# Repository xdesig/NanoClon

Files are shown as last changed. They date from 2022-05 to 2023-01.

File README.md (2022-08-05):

# NanoClon V 0.01   

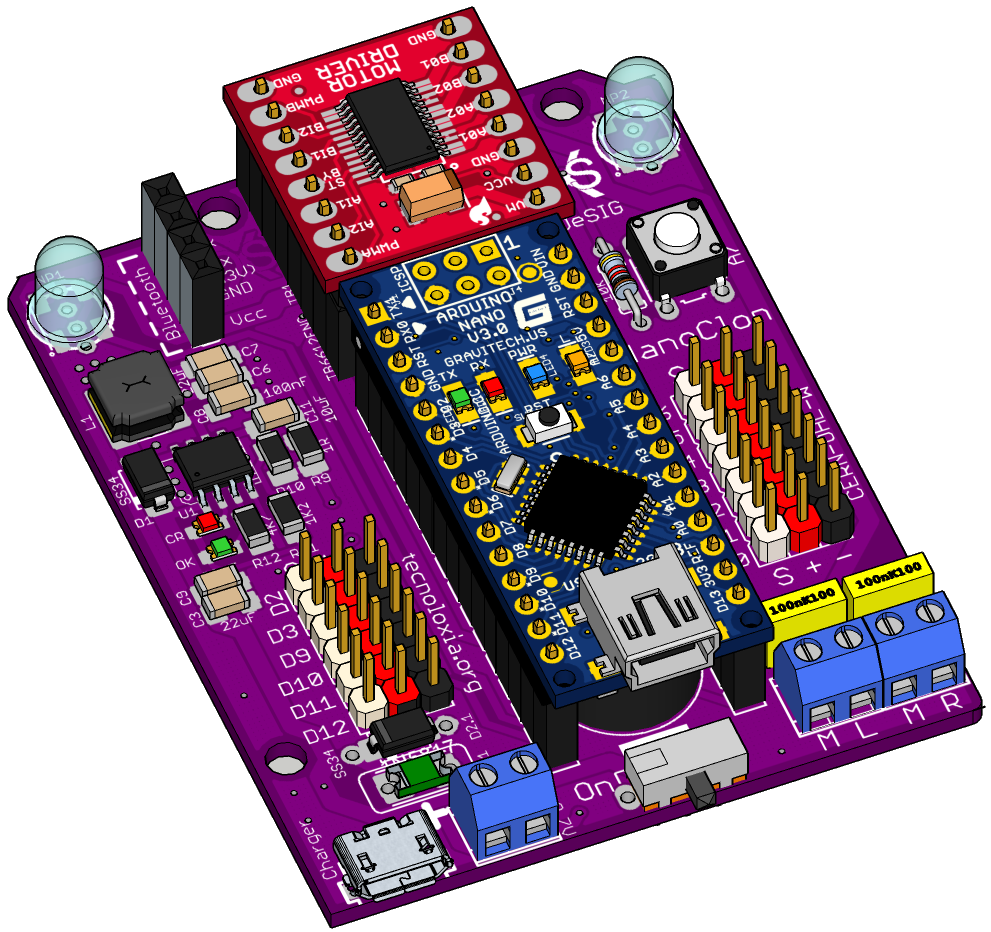
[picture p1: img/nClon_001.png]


## initial version.
Circuit that has everything you need to assemble your mClon-style robot, 
avoiding having to look for the missing Arduino one from RobotDyn that 
was used in the ShieldClon version.

The components can be SMD or THT, except for the Step-Up circuit/Lipo 
battery charge controller which is SMD,  with 1206 and 0805 components
larger than the usual 0603 and 0402).
You can an option not solder the smd components of the step-up,
and use a power bank by simply soldering the Bat-Vcc selector on the underside.

### [Assembly manual][Man]

#### Deseñado en Estrimia con agarimo.

## Author and license
* Author: [XDeSIG][TWI01]
* License:[CERN Open Hardware Licence Version 2 - Weakly Reciprocal][CERN-OHL-W]


## To buy boards

Developer don't produce boards to sell. Under [_provider_][provider]
directory there are instructions to order yourself.

<!-- links -->
[Man]: https://github.com/xdesig/NanoClon/blob/main/docs/nClon_001_Montaxe.pdf
[tecnoloxia.org]: https://tecnoloxia.org/mclon/que-e-mclon/
[CERN-OHL-W]: https://ohwr.org/cern_ohl_w_v2.pdf
[TWI01]: https://twitter.com/xdesig
[provider]: https://www.pcbway.com/project/shareproject/W50475ASJ144_NanoClon_001_gerber_f511f448.html

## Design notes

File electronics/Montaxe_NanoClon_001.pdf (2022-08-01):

# nClon

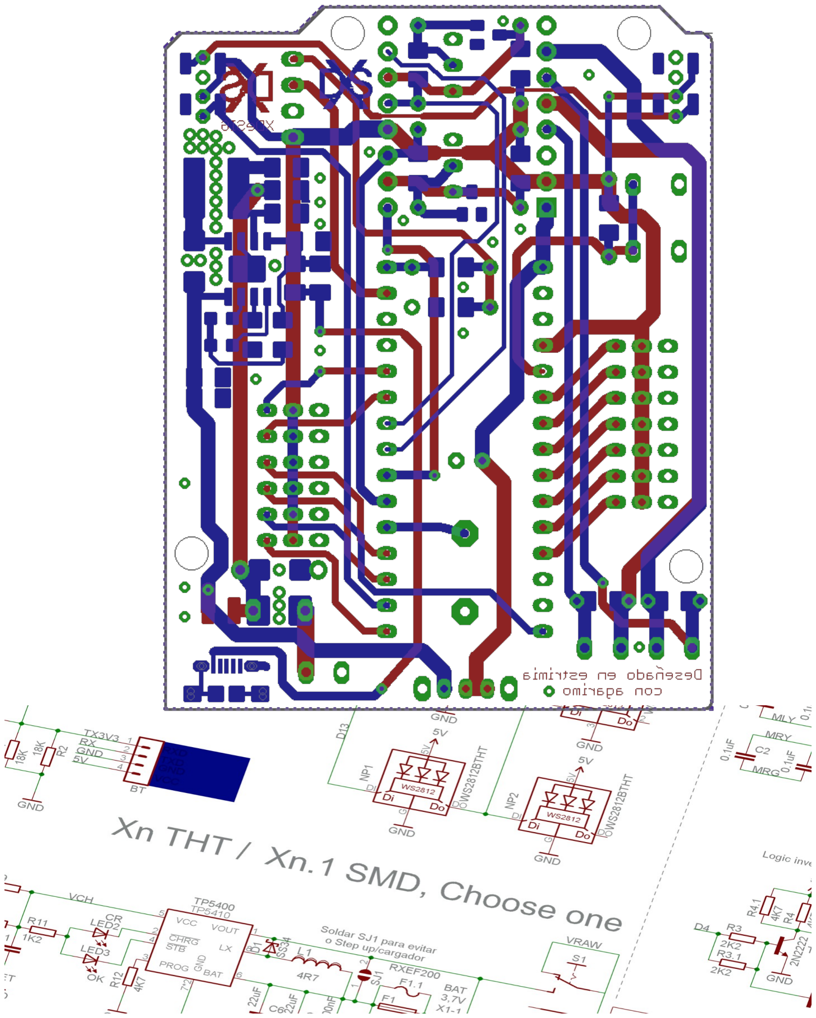
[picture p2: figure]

nClon | Manual de montaxe

Este circuíto ten todo o que precisamos () para construír o teu robot estilo mClon de @tecnoloxia, evitando ter que buscar o Arduino de RobotDyn (xa non se fabrica) que se utilizou na versión de ShieldClon.

Os compoñentes poden ser SMD ou THT, excepto o controlador de carga de batería Lipo/Step-Up que é SMD, con compoñentes 1206 e 0805 máis grandes que os habituais 0603 e 0402).
Podes optar por non soldar os compoñentes do cargador/elevador smd e usar un banco de enerxía, simplemente facendo unha pequena soldadura no selector Bat-Vcc que se atopa parte inferior.

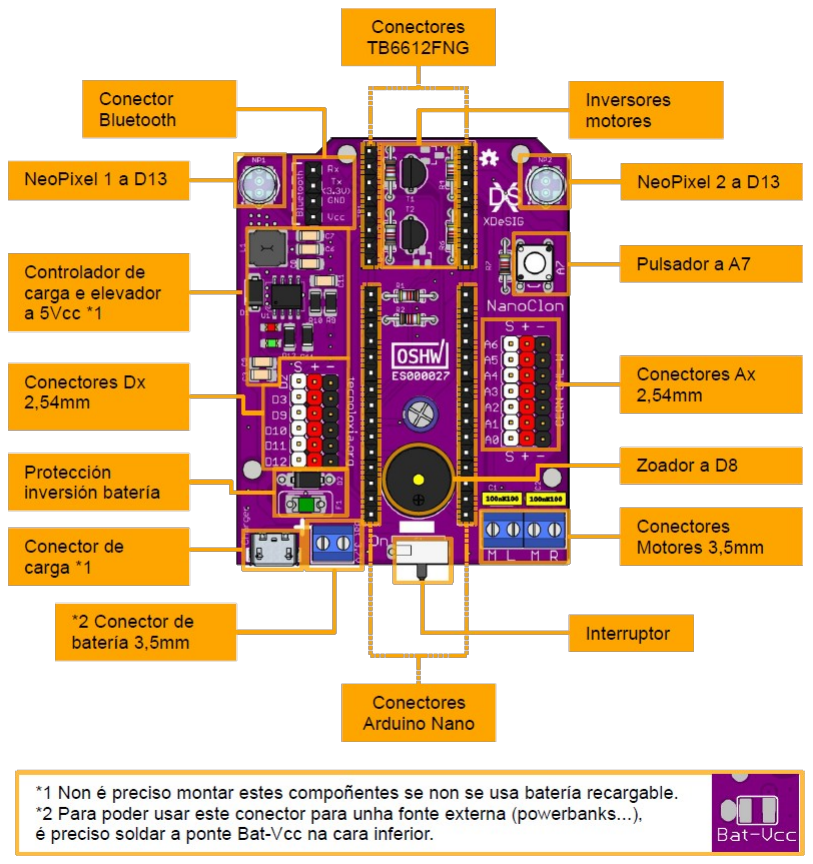
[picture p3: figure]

Podes atopar máis información en https://github.com/xdesig/NanoClon e https://tecnoloxia.org/mclon/

Deseñado en Estrimia con agarimo. | Pax. 2 de 12 | XdeSIG 2022. (CC BY-SA 4.0) Rev. 00

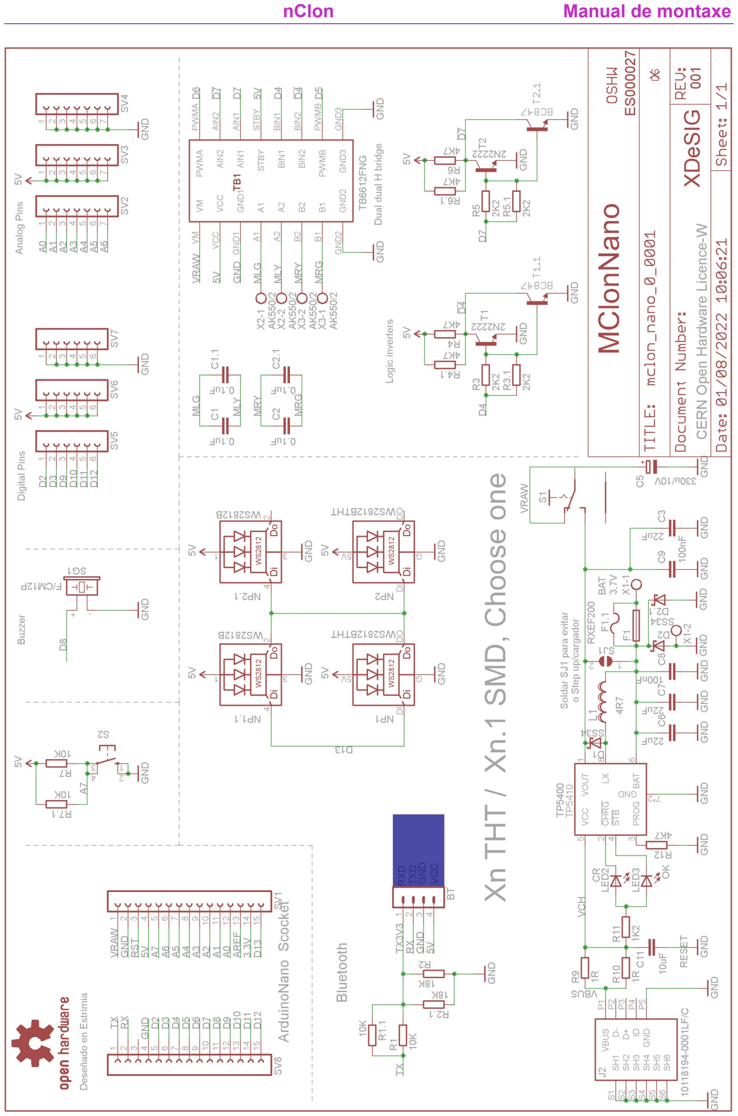
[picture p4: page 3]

Deseñado en Estrimia con agarimo. | Pax. 3 de 12 | XdeSIG 2022. (CC BY-SA 4.0) Rev. 00

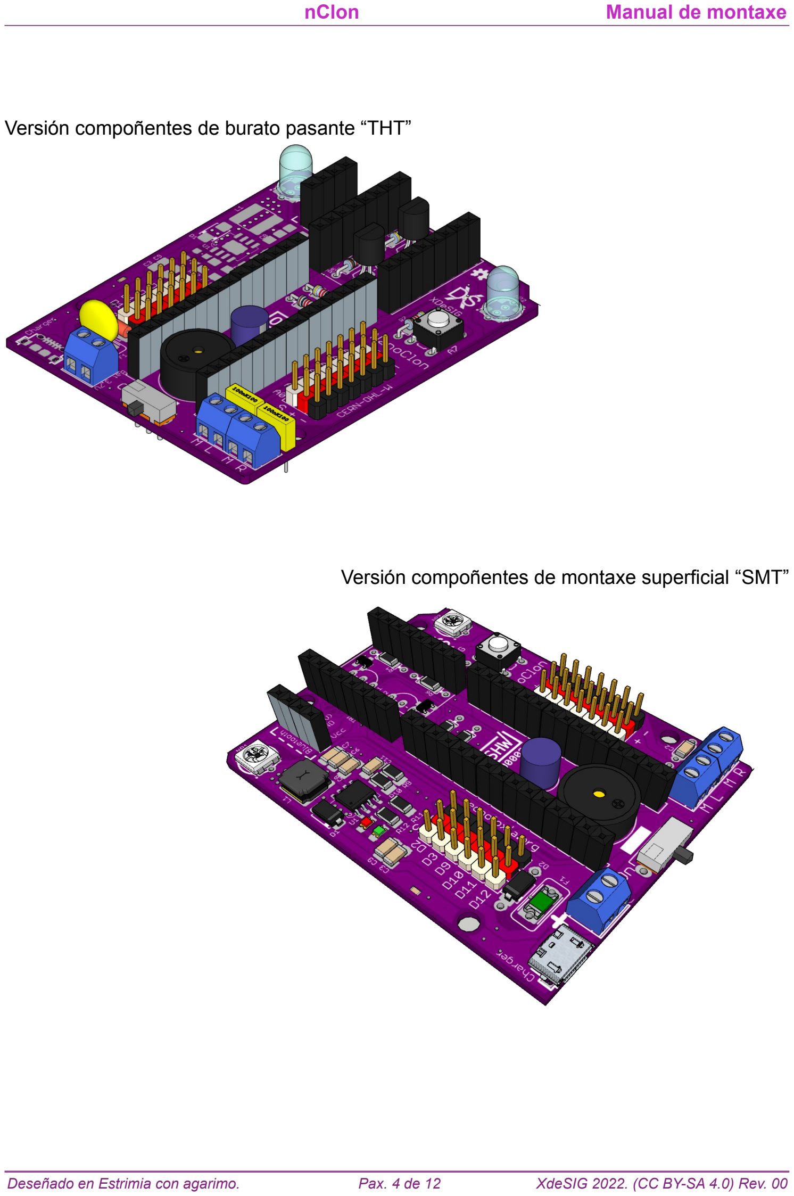
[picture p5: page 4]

Versión compoñentes de burato pasante “THT”

Versión compoñentes de montaxe superficial “SMT”

Deseñado en Estrimia con agarimo. | Pax. 4 de 12 | XdeSIG 2022. (CC BY-SA 4.0) Rev. 00

- Inventario de compoñentes comúns as dúas versións.

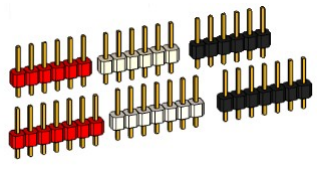
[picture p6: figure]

- Tiras de postes
- 1x 6 x 2,54mm Vermella
- 1x 6 x 2,54mm Branca
- 1x 6 x 2,54mm Negra
- 1x 7 x 2,54mm Vermella
- 1x 7 x 2,54mm Branca
- 1x 7 x 2,54mm Negra

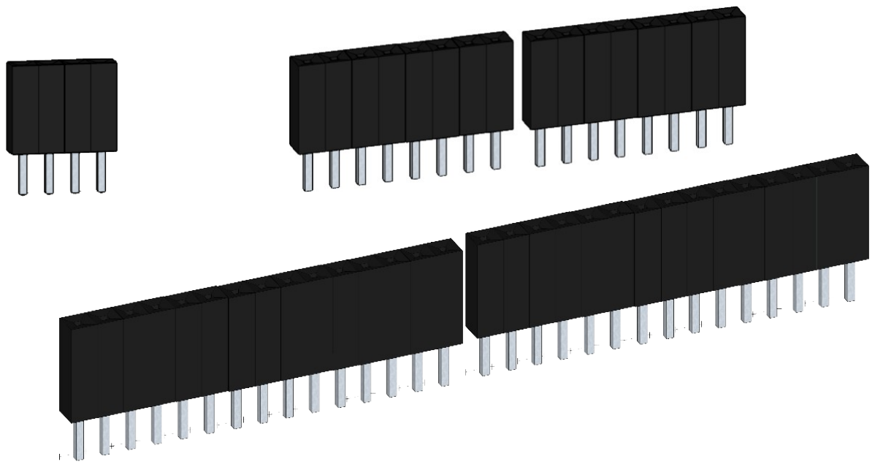
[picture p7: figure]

- Tiras Femia
- 1x 4 x 2,54mm
- 2x 8 x 2,54mm
- 2x 15 x 2,54mm
- Bloques terminais
- 3 x 2 x 3,5mm
- Interruptor SK-12D07 e pulsador 6 x 6mm

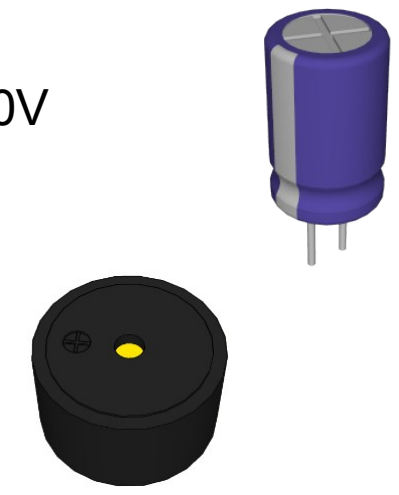
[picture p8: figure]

### - Condensador electrolítico 330µF/10V

- 6.3x7mm

### - Zoador 12mm 3,6V~5V

Deseñado en Estrimia con agarimo. | Pax. 5 de 12 | XdeSIG 2022. (CC BY-SA 4.0) Rev. 00

- Inventario de compoñentes para a versión de burato pasante “THT”
- Resistencias:
- 2x 2K2W, 2x 4K7W, 2x 10KW, 1x 18KW.
- Condensadores:
- 2x 100nF/≥16V,
- Fusible 1x Polyfuse 0,5mA
- Díodo SCHOTTKY 1N5817
- Transistores:
- 2x 2N2222
- 2x LEDes NeoPixel 5mm WS2812BTH
- Inventario de compoñentes para a versión montaxe superficial “SMD”
- Resistencias 1206:

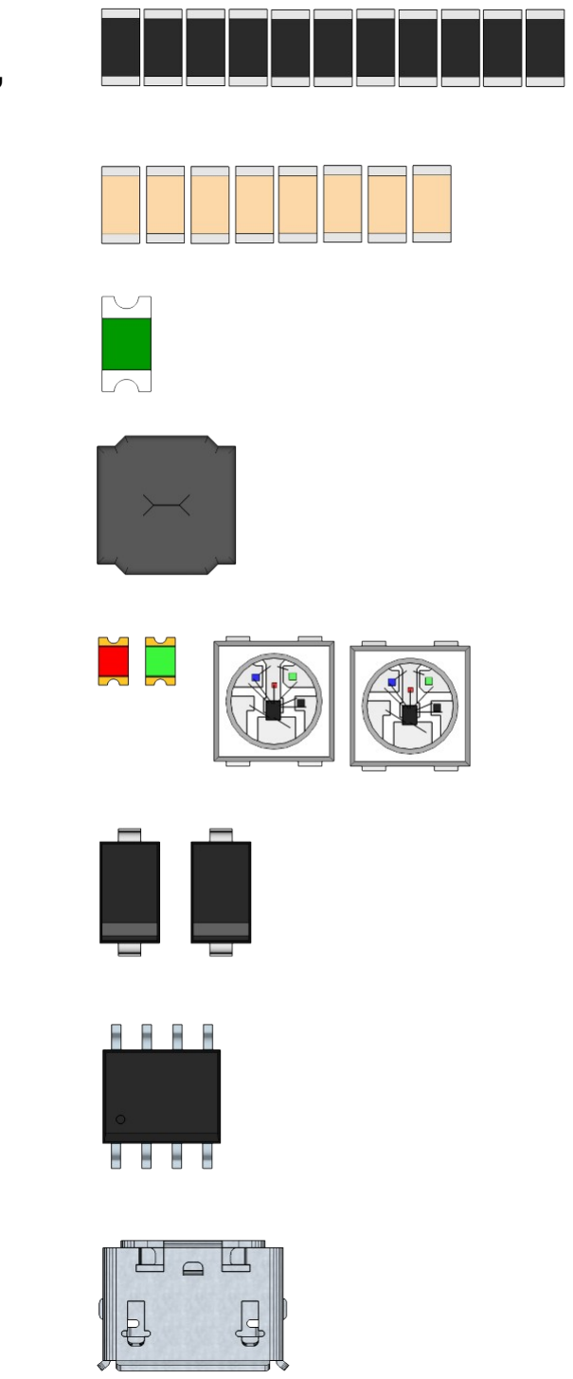
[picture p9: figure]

- 2x 1W, 1x 1K2, 1x 2K2W 3x 4K7W, 1x 18KW,
2x 10KW.
- Condensadores 1206:
- 4x 100nF, 3x 22uF/10V, 1x10uF/10V
- Fusible rearmable 1206/1210.
- MF-NSMF200-2
- Indutancia SMD 6x6mm:
- 4R7(4.7uH ±30% )
- LEDes:
- 2x LED 0805:
- Vermello e verde
- 2x NeoPixeles WS2812B
- Díodos SCHOTTKY SMA:
- 2x SS34
- Controlador batería/Step-Up SOIC-8
- 1x TP5400.
- Conector USB
- MicroXNJ .
Deseñado en Estrimia con agarimo. | Pax. 6 de 12 | XdeSIG 2022. (CC BY-SA 4.0) Rev. 00

- Módulos:
- Ponte “H” Dual
- Arduino Nano
- PCB

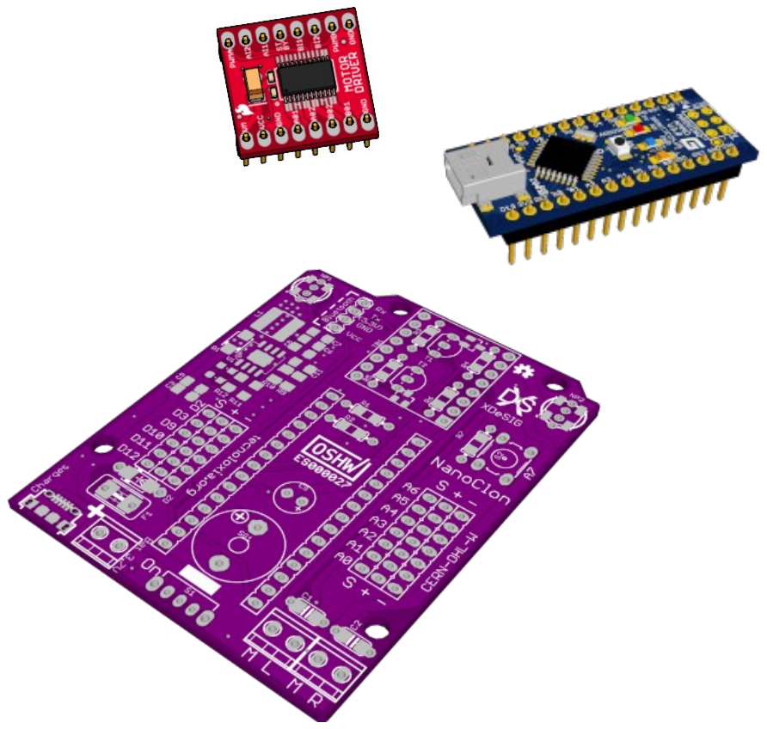
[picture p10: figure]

Primeiro imos montar a versión de compoñentes de burato pasante THT

- A montaxe, comeza polos compoñentes de baixo perfil, as resistencias. A placa vén serigrafíada cos valores dos compoñentes.
Vai soldando unha a unha as resistencias, orientadas de tal forma que sexan fáciles de ler, deixando a banda de tolerancia na dereita (a máis separada), vai cortando o sobrante das patas cada vez que soldes unha resistencia.
- OLLO As cores representadas nas resistencias non se corresponden co seu Valor

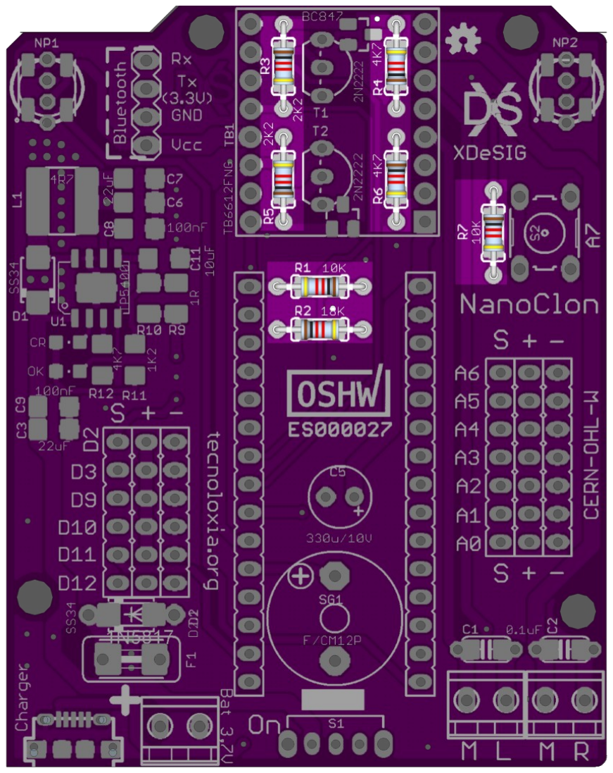
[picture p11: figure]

Deseñado en Estrimia con agarimo. | Pax. 7 de 12 | XdeSIG 2022. (CC BY-SA 4.0) Rev. 00

- Pasamos a soldar o díodo D2 Schottky 1N5817 ou compatible, este compoñente ten polaridade, faremos coincidir a liña que marca o cátodo coa marca da serigrafía:
- Na placa atopamos textos como D2... e D2 o primeiro refírese o sinal dixital do Arduino, o

segundo o atopamos o lado do compoñente 1N5817, indicando que é o Díodo 2...

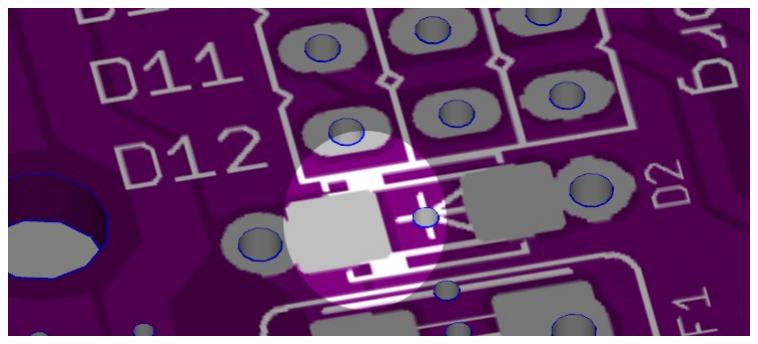
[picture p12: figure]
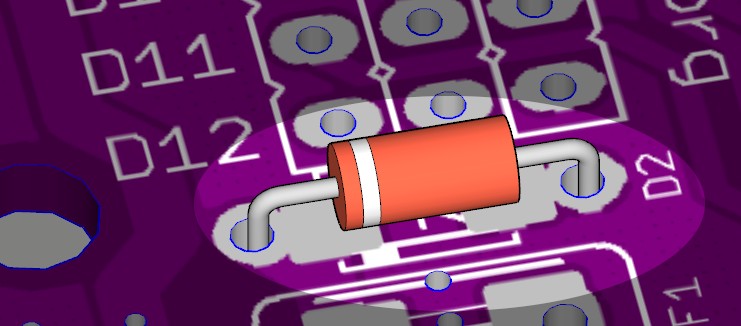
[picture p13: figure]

O soldar os semicondutores teremos que ter coidado de non aplicar moito calor

durante moito tempo, estes só aguantan uns 300º durante 10 segundos como máximo.

- Continuamos soldando o interruptor e o pulsador, estes non teñen polaridade

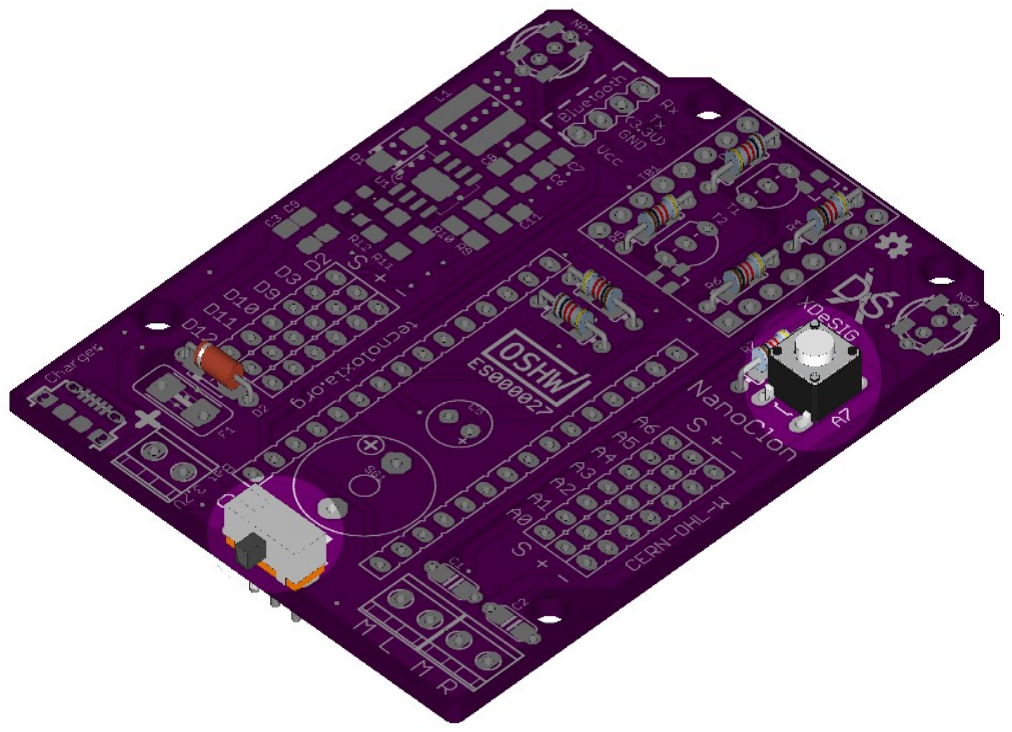
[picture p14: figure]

O pulsador, so ten unha orientación.

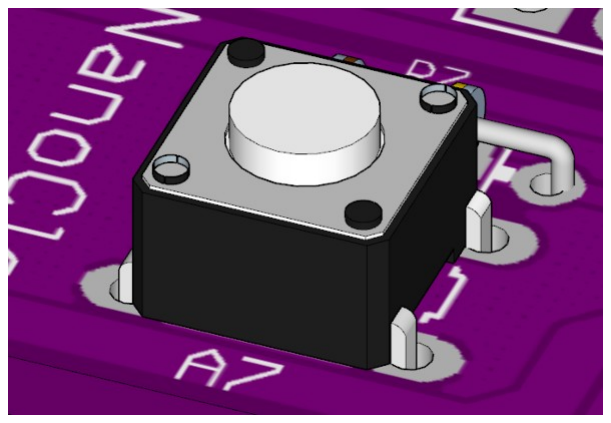
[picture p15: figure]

Deseñado en Estrimia con agarimo. | Pax. 8 de 12 | XdeSIG 2022. (CC BY-SA 4.0) Rev. 00

- Soldamos agora as tiras de postes, prestando atención as cores e que queden verticais:

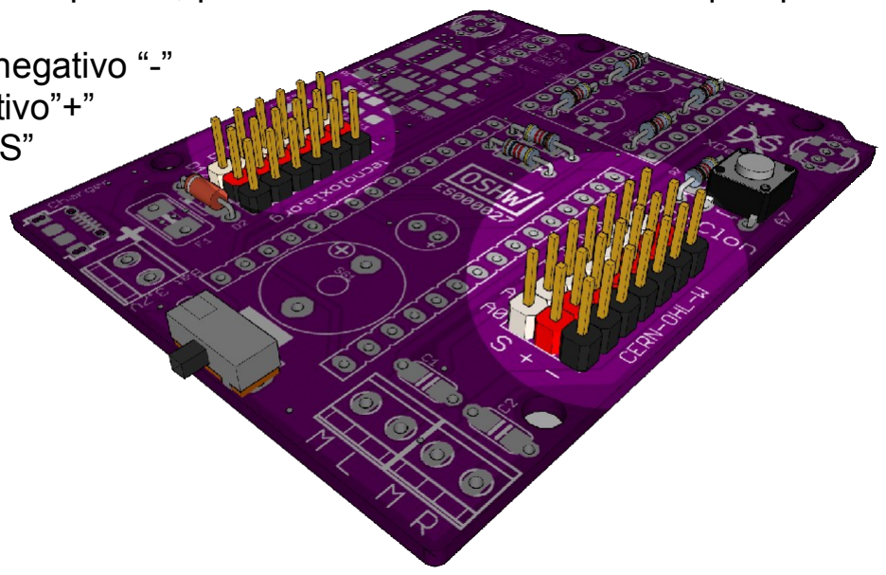
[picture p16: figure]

- Negro(preto) para o negativo “-”
- Vermello para o positivo”+”
- Branco para o sinal “S”
- Seguidamente soldamos os transistores T1 e T2, atentos a serigrafía, e coidade de non pasarnos ca calor e tempo de soldadura.
- Consello: Solda unha pata de un transistor, e mentas soldas a do outro, este arrefriase un pouco.

Só aguantan uns 300º durante 10 segundos

como máximo.

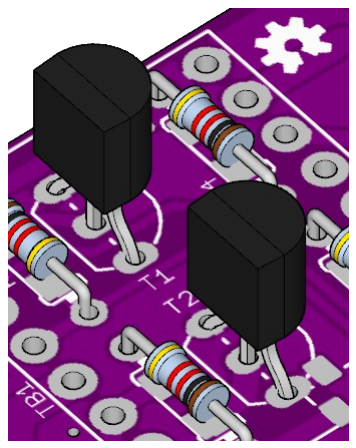
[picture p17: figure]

- Antes de continuar comproba que o condensador C5 non é máis alto que as tiras de conexión do Arduino. No caso de que sexa máis alto teremos que soldalo tumbado no seguinte paso
- Soldamos o condensador C5, este compoñente ten polaridade.
Na placa ven marcada a pata positiva ”+”, pero o condensador ten marcada

(xeralmente) a pata negativa “-” con unha franxa.

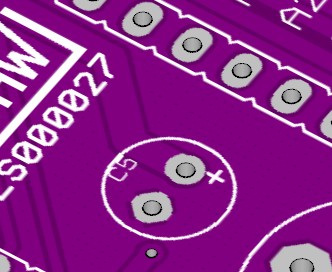
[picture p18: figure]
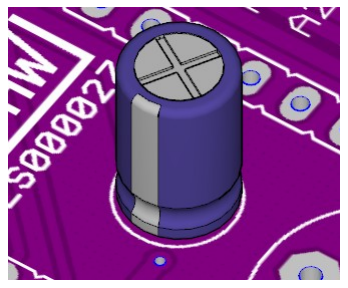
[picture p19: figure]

Deseñado en Estrimia con agarimo. | Pax. 9 de 12 | XdeSIG 2022. (CC BY-SA 4.0) Rev. 00

- E soldamos o coador que tamén ten polaridade, este ten marcada a pata positiva (+)

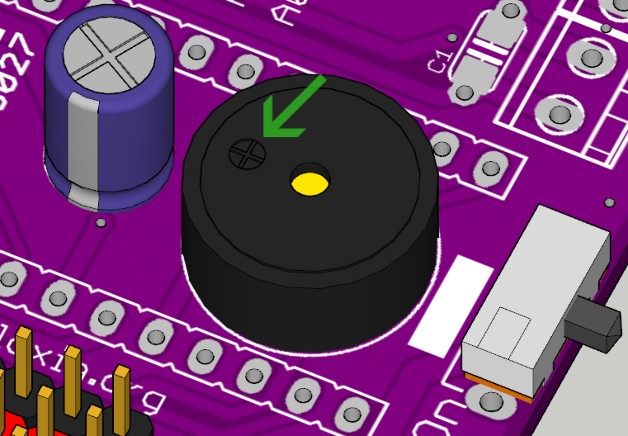
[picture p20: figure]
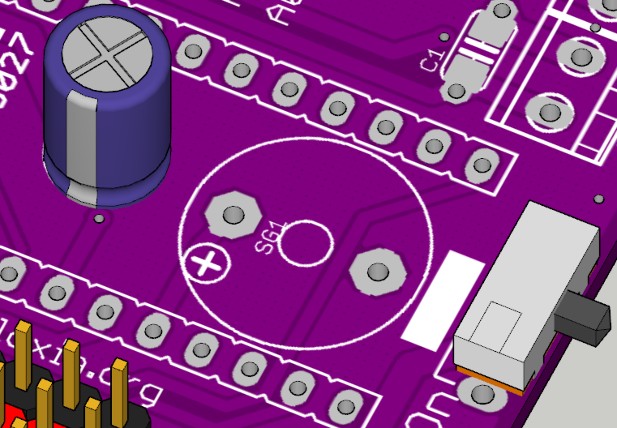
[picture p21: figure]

- Xa podemos soldar os conectores da batería e motores, non teñen polaridade, pero deixa a entrada do cable o borde da placa ;-).

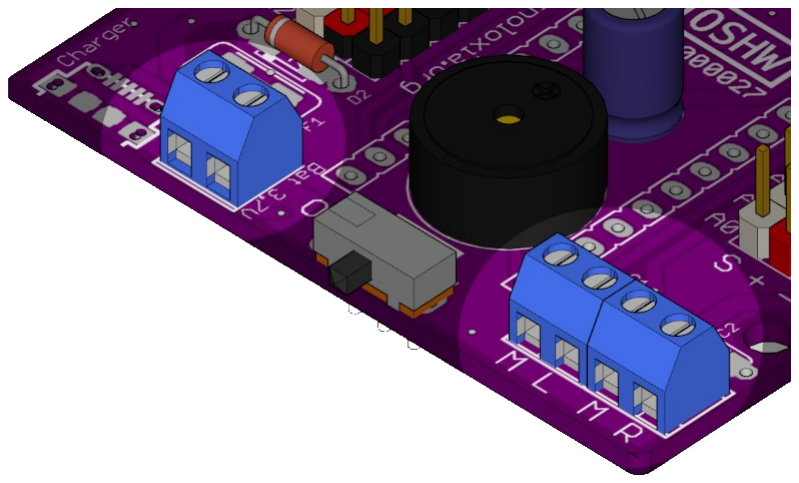
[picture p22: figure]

- Soldaremos agora fusible rearmable e os condensadores dos motores.

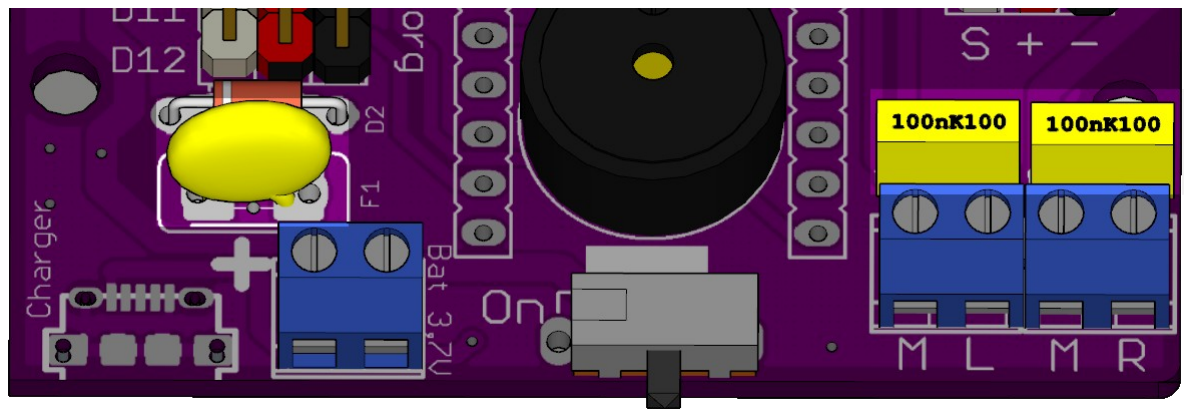
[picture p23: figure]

Deseñado en Estrimia con agarimo. | Pax. 10 de 12 | XdeSIG 2022. (CC BY-SA 4.0) Rev. 00

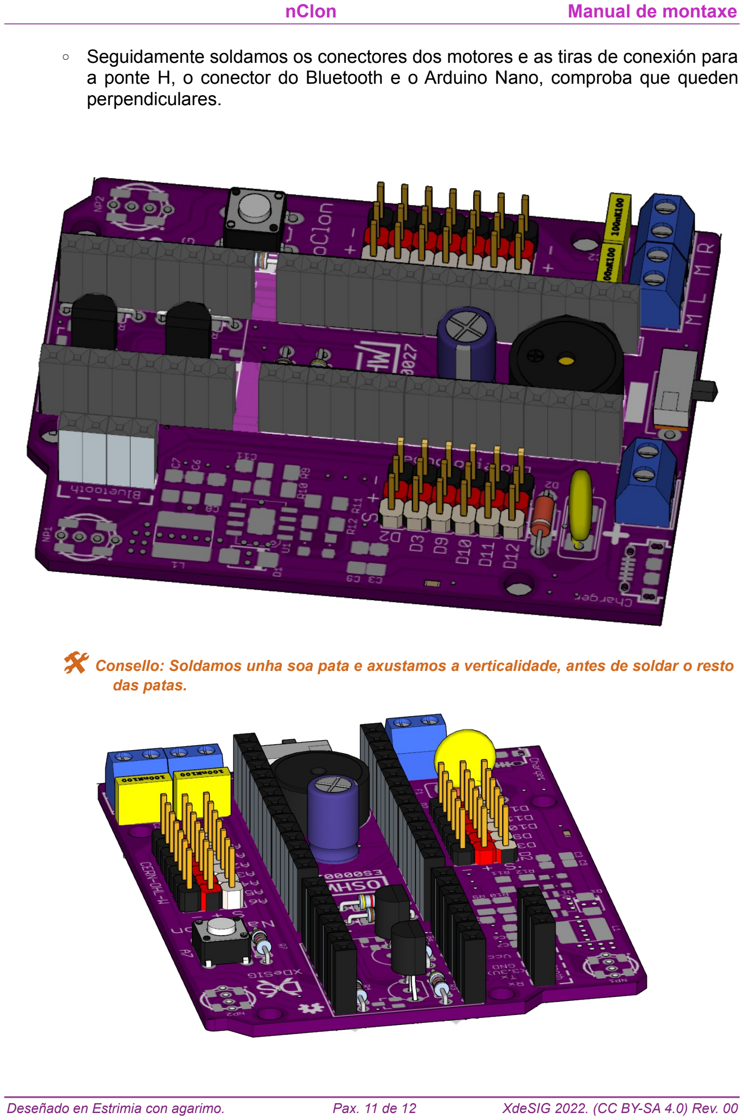
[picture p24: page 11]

- Seguidamente soldamos os conectores dos motores e as tiras de conexión para a ponte H, o conector do Bluetooth e o Arduino Nano, comproba que queden perpendiculares.
- Consello: Soldamos unha soa pata e axustamos a verticalidade, antes de soldar o resto das patas.
Deseñado en Estrimia con agarimo. | Pax. 11 de 12 | XdeSIG 2022. (CC BY-SA 4.0) Rev. 00

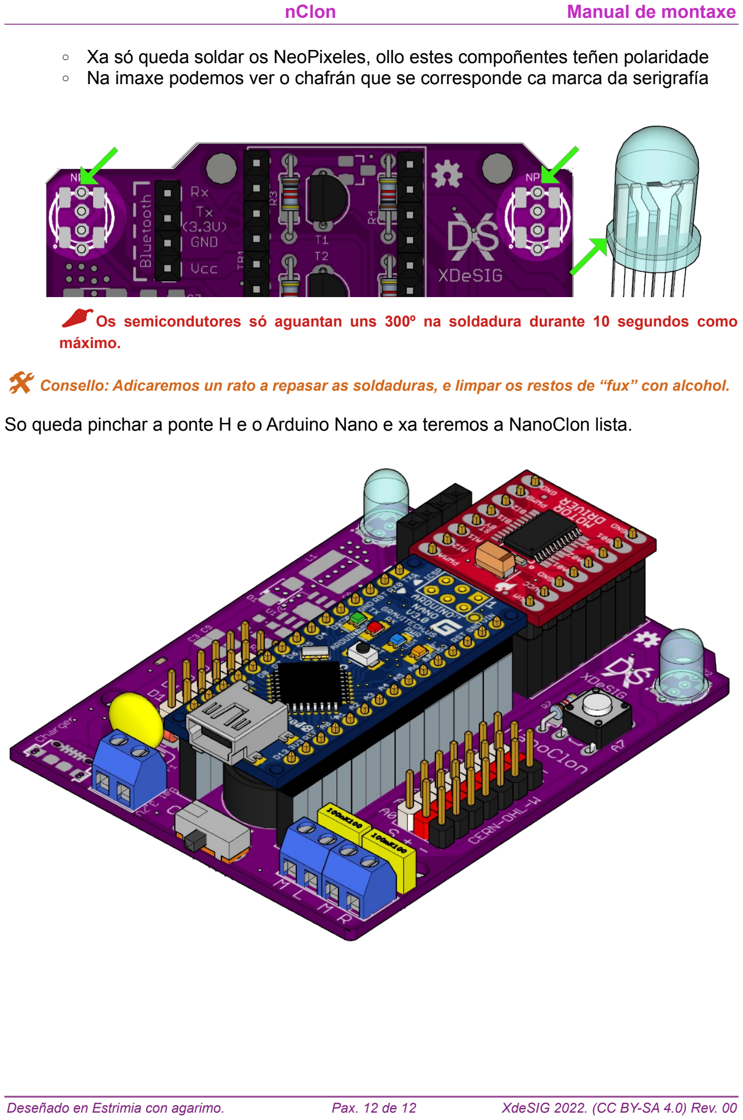
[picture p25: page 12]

- Xa só queda soldar os NeoPixeles, ollo estes compoñentes teñen polaridade
- Na imaxe podemos ver o chafrán que se corresponde ca marca da serigrafía

Os semicondutores só aguantan uns 300º na soldadura durante 10 segundos como

máximo.

- Consello: Adicaremos un rato a repasar as soldaduras, e limpar os restos de “fux” con alcohol.

So queda pinchar a ponte H e o Arduino Nano e xa teremos a NanoClon lista.

Deseñado en Estrimia con agarimo. | Pax. 12 de 12 | XdeSIG 2022. (CC BY-SA 4.0) Rev. 00

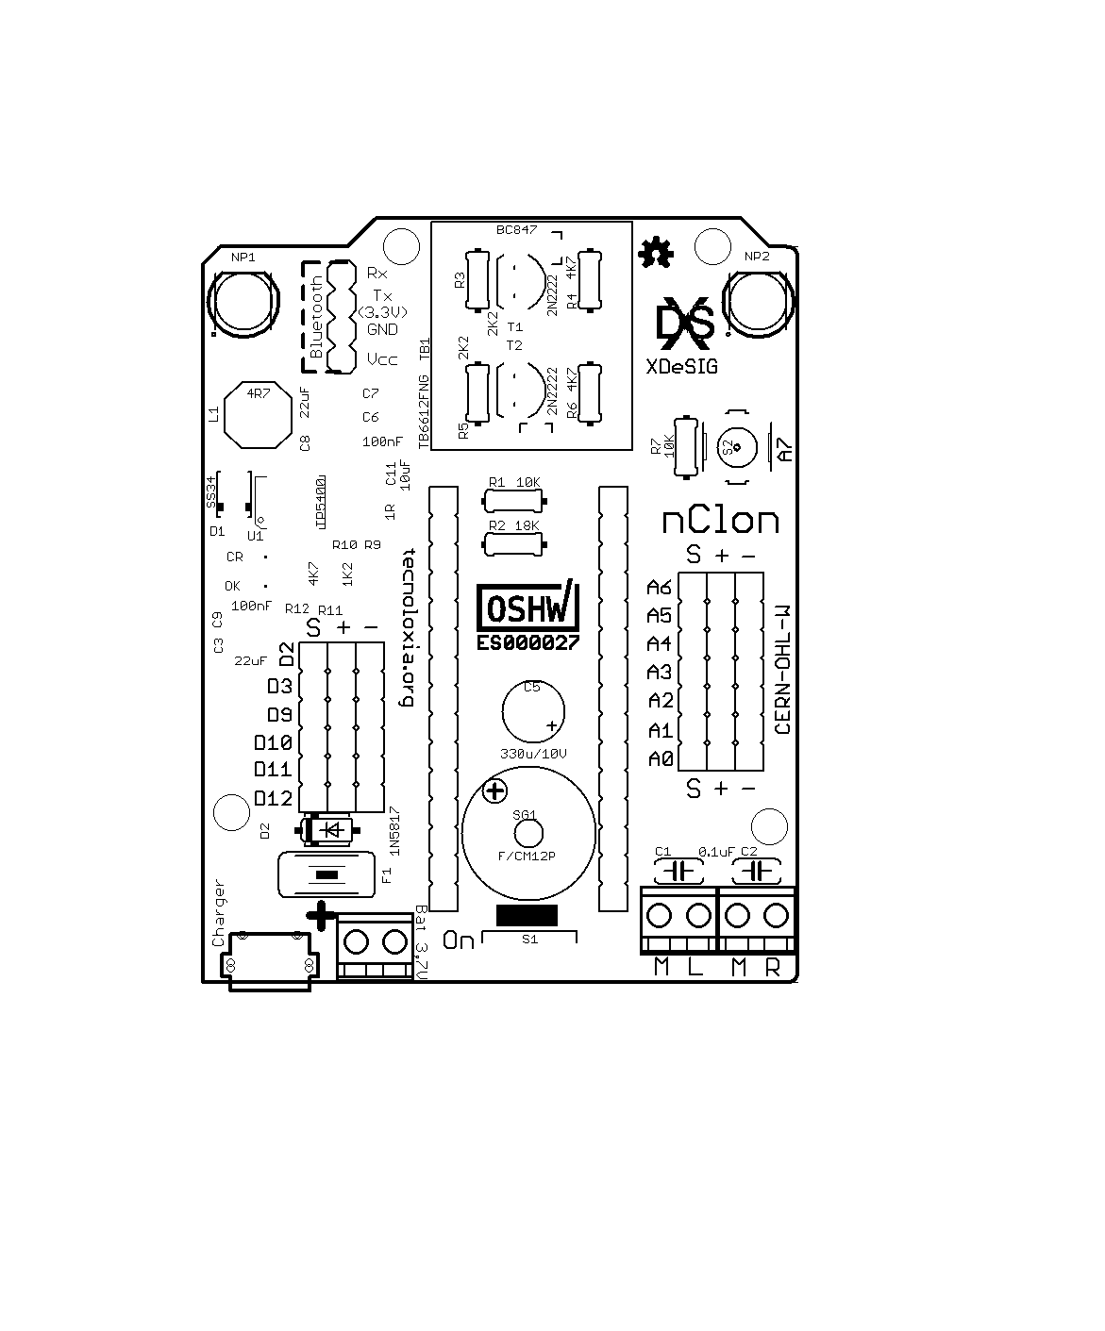
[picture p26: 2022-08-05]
img/nClon_001_SilkTop.png

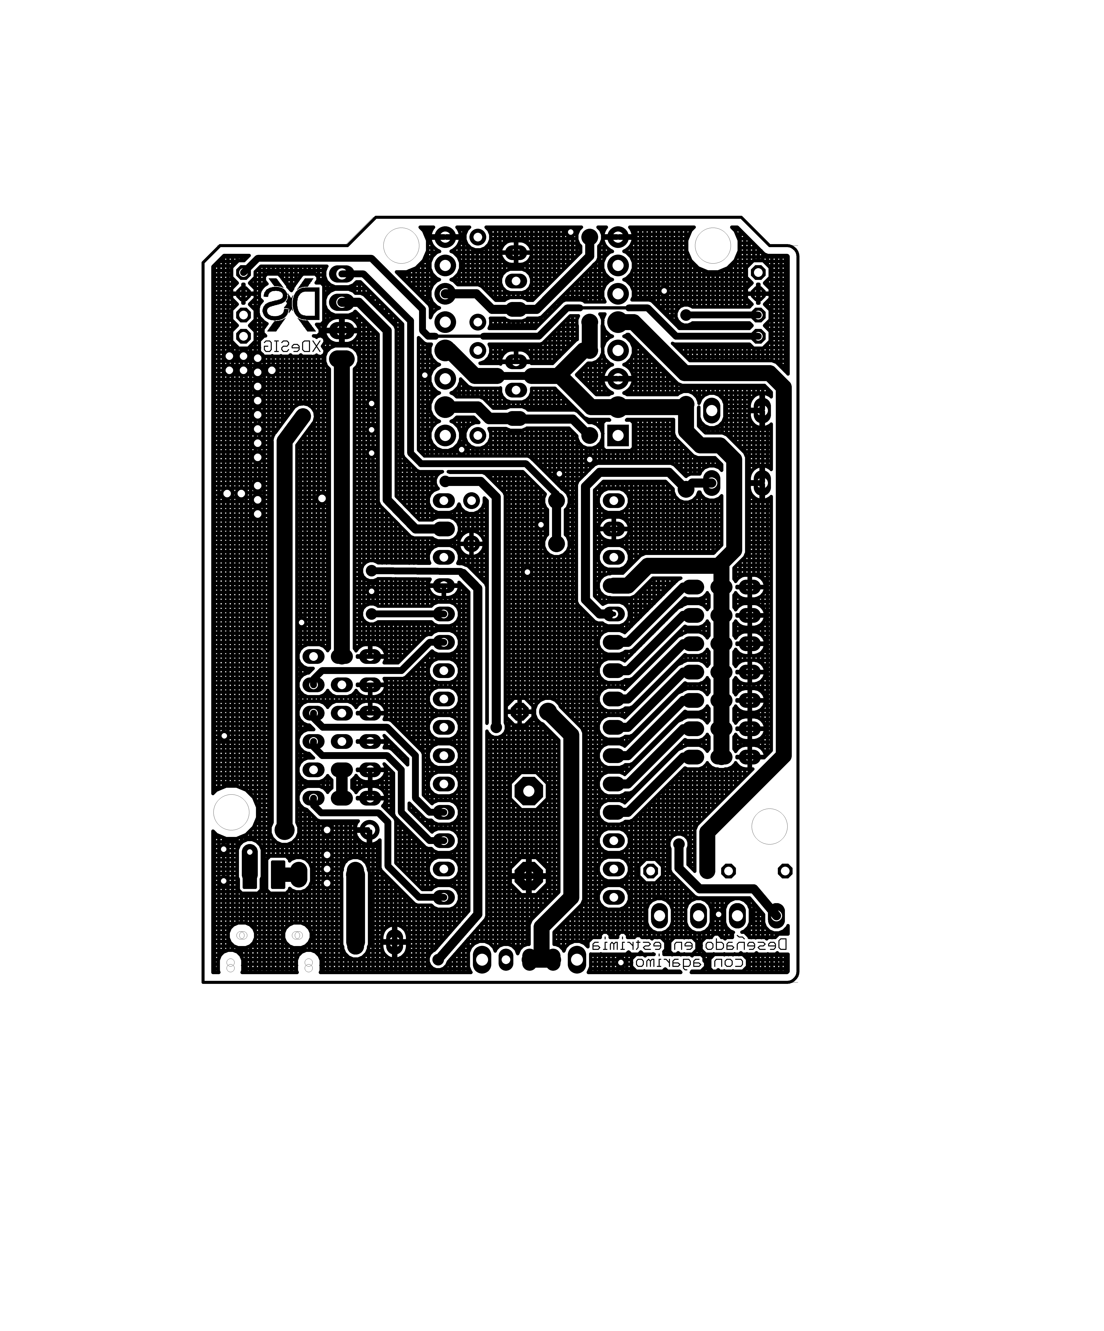
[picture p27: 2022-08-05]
img/nClon_001_CopBot.png

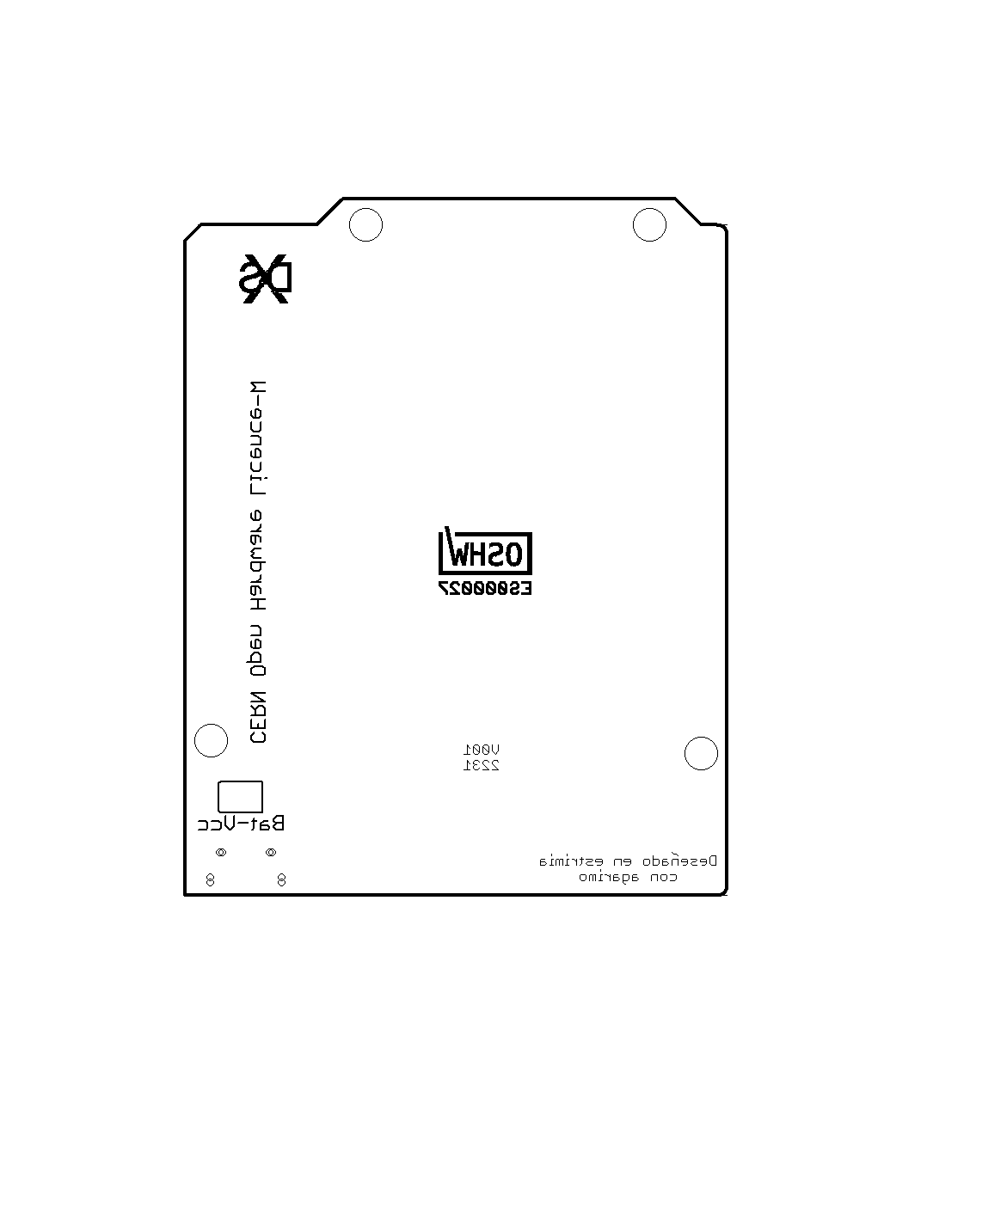
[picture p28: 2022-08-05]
img/nClon_001_SilkBot.png

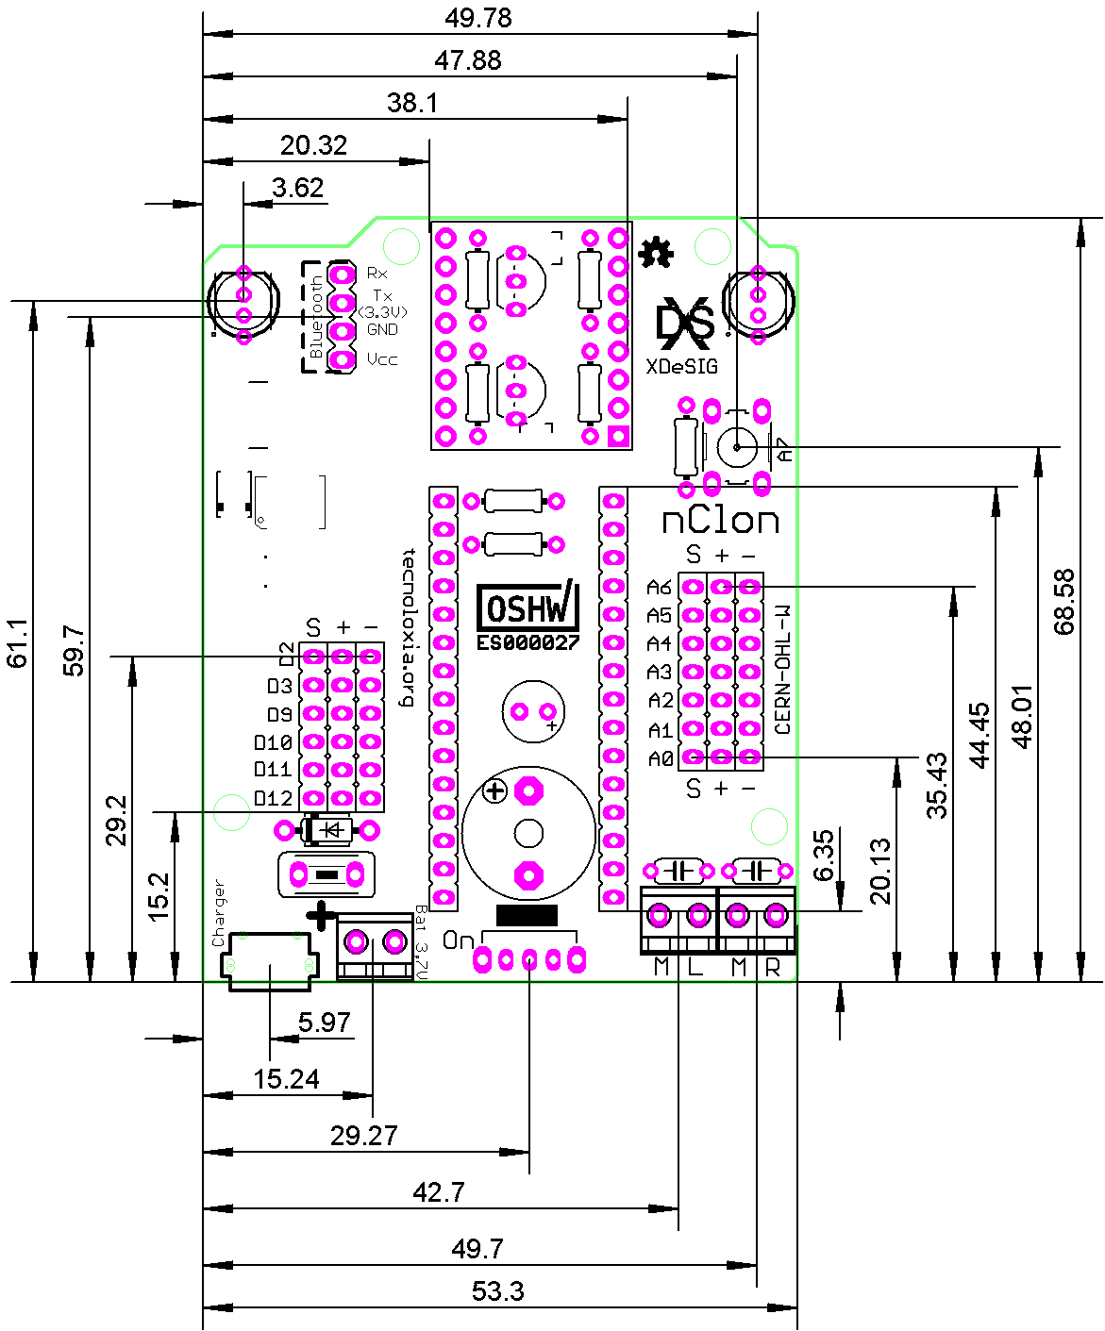
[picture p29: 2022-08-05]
img/nClon_001_MEAS.png

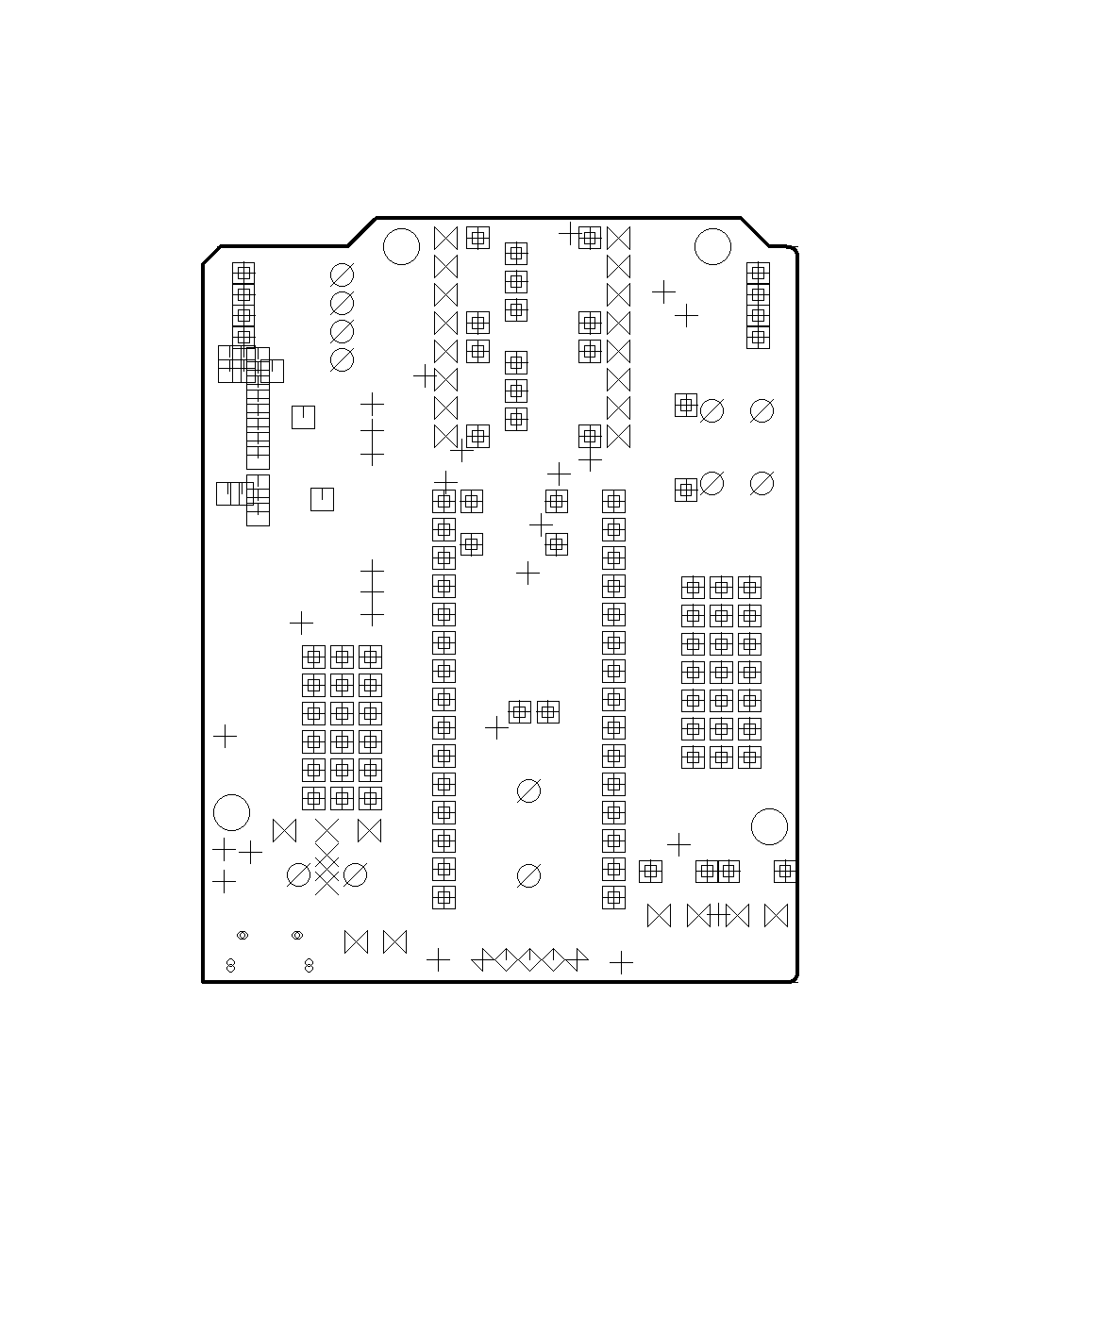
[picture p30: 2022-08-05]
img/nClon_001_Drills.png

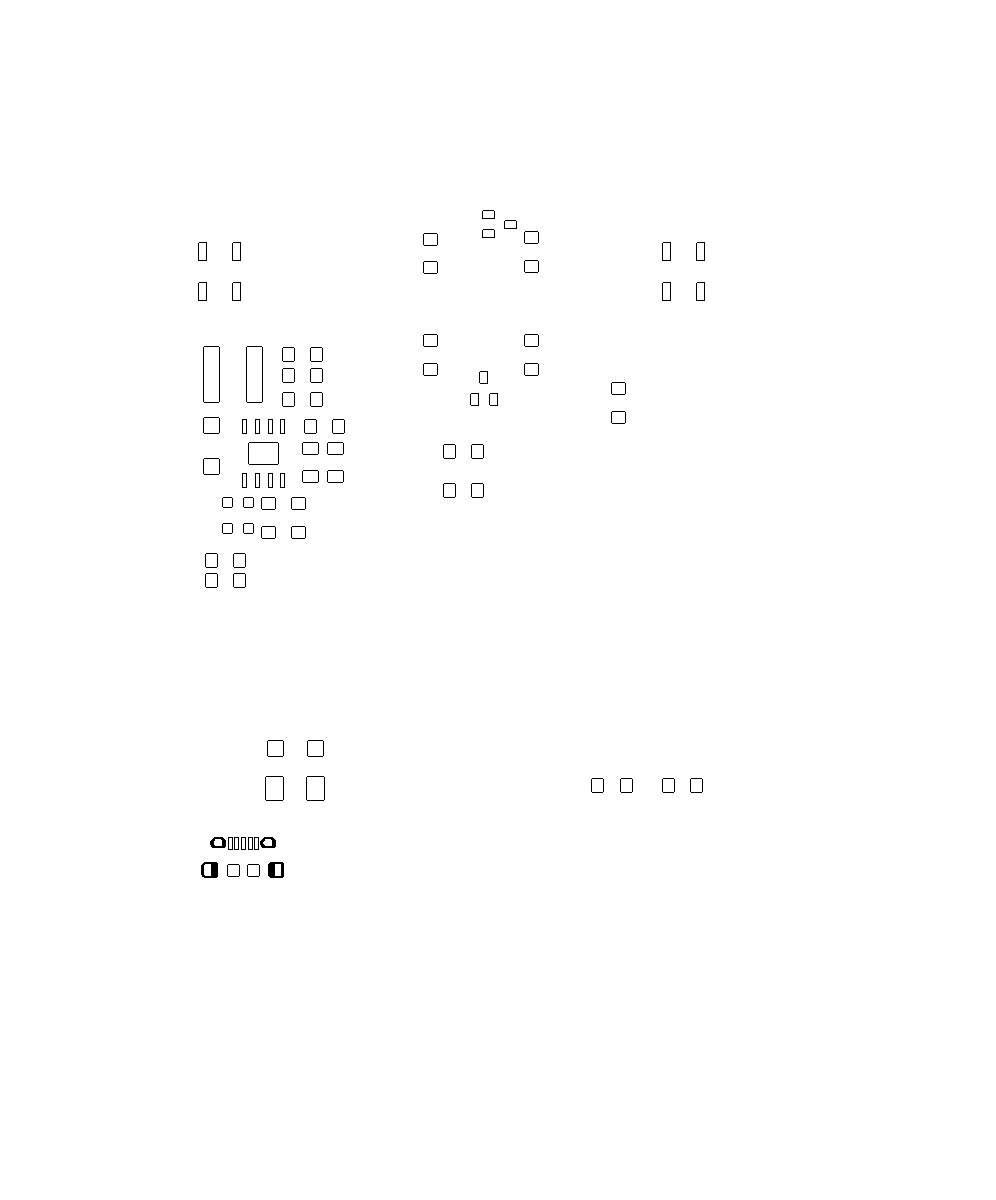
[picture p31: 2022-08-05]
img/nClon_001_CreTop.png

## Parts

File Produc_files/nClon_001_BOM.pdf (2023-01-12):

1 | | S2 | 10-XX | B3F-1000 | TS665CJ (https://www.lcsc.com/product-detail/Tactile-Switches_SHOU-HAN-TS665CJ_C393938.html)
2 | | SV1, SV8 | CON-LSTA_FE15-1 | CON-LSTA_FE15 | C124408 (https://www.lcsc.com/product-detail/Female-Headers_Ckmtw-Shenzhen-Cankemeng-B-2200S15P-A120_C124408.html)
1 | | S1 | SK12F14 | SK12F14G5 | SK12F14G5 (https://www.lcsc.com/product-detail/Slide-Switches_SHOU-HAN-SK12F14G5_C2887263.html)
3 | | SV5, SV6, SV7 | FE06-1 | FE06 | C37208 (https://www.lcsc.com/product-detail/Pin-Headers_BOOMELE-Boom-Precision-Elec-C37208_C37208.html) | | SV5 White, SV6 Reed, SV7 Black
3 | | SV2, SV3, SV4 | FE07-1 | FE07 | DZ254R-11-0 (https://www.lcsc.com/product-detail/Pin-Headers_DEALON-DZ254R-11-07-63_C2935913.html) | | SV2 White, SV3 Reed, SV4 Black
1 | | BT | MA04-1 | MA04-1 | C2718488 (https://www.lcsc.com/product-detail/Female-Headers_BOOMELE-Boom-Precision-Elec-C2718488_C2718488.html)
1 | 1N5817 | D2 | DIODE_SCHOTTKY | DO35-7 | C698892 (https://www.lcsc.com/product-detail/Schottky-Barrier-Diodes-SBD_Yangzhou-Yangjie-Elec-Tech-1N5817_C698892.html) | | Act 12/01/23
2 | 0.1uF | C1, C2 | 100nF/50V 5mm | C050-024X044 | C2896059 (https://www.lcsc.com/product-detail/Ceramic-Disc-Capacitors_SHM-DCS104M26Y5UF50L5A0_C2896059.html)
1 | 330u/10V | C5 | CPOL-EUE2.5-6 | E2,5-6 | C399138 (https://www.lcsc.com/product-detail/Aluminum-Electrolytic-Capacitors-Leaded_Xunda-T73371AMD075RB_C399138.html)
2 | 4K7 | R4, R6 | R-EU_0204/7 | 0204/7 | C119339 (https://www.lcsc.com/product-detail/Through-Hole-Resistors_CCO-Chian-Chia-Elec-MF1-4W-4-7K-1-T52_C119339.html)
2 | 10K | R1, R7 | 10K/0,25W | 0204/7 | C172967 (https://www.lcsc.com/product-detail/Through-Hole-Resistors_YAGEO-MFR-25FTE52-10K_C172967.html)
1 | 18K | R2 | 18K/0,25W | 0204/7 | C410668 (https://www.lcsc.com/product-detail/Through-Hole-Resistors_TyoHM-RN-1-4W-18K-F-T-B-A1_C410668.html)
2 | 2K2 | R3, R5 | R-EU_0204/7 | 0204/7 | C714002 (https://www.lcsc.com/product-detail/Through-Hole-Resistors_Huaxing-Mechanical-Elec-MF1-4W-2-2K-1-T52_C714002.html)
2 | 2N2222 | T1, T2 | 2N2222 | TO92-EBC-OVAL | C118536 (https://www.lcsc.com/product-detail/Bipolar-Transistors-BJT_ST-Semtech-2N2222A_C118536.html)
3 | KF350-2 | X1, X2, X3 | KF350-2 | KF350-2 | C474892 (https://www.lcsc.com/product-detail/Screw-terminal_Cixi-Kefa-Elec-KF350-3-5-2P_C474892.html)
1 | F/CM12P | SG1 | F/CM12Pasive | 12mm | C252921 (https://www.lcsc.com/product-detail/Buzzers_INGHAi-GMC1209YB-25R2048_C252921.html) | | Magnetic 2.5V~5V 3.6V 2048Hz
1 | RXEF200 | F1 | FUSETE5 | 5,1mm / 6,2mm Ih > 500mA | C506879 (https://www.lcsc.com/product-detail/Resettable-Fuses_TLC-Electronic-TRA075Z-L_C506879.html)
1 | TB6612FNG | TB1 | TB6612FNG | TB6612FNG | # | TB6612FNG (https://es.aliexpress.com/item/32223093678.html) | Driver Motor
2 | WS2812BTHT | NP1, NP2 | WS2812BTHT | NEOPIXEL5MM | # | WS2812BTHT (https://es.aliexpress.com/item/32714487459.html) Neo Pixel
1 | Nano | # | Arduino Nano | 2 x 15 | # | Arduino Nano (https://store.arduino.cc/products/arduino-nano)
4 | 0.1uF | C1.1, C2.1, C8, C9 | C-EUC1206 | C1206 | C110255 (https://www.lcsc.com/product-detail/Multilayer-Ceramic-Capacitors-MLCC-SMD-SMT_FH-Guangdong-Fenghua-Advanced-Tech-1206B104K101NT_C110255.html) | Act 12/01/23
3 | 22uF | C3, C6, C7 | C-EUC1206 | C1206 | C12891 (https://www.lcsc.com/product-detail/Multilayer-Ceramic-Capacitors-MLCC-SMD-SMT_Samsung-Electro-Mechanics-CL31A226KAHNNNE_C12891.html) | Act 12/01/23
1 | 10uF | C11 | C-EUC1206 | C1206 | C13585 (https://www.lcsc.com/product-detail/Multilayer-Ceramic-Capacitors-MLCC-SMD-SMT_Samsung-Electro-Mechanics-CL31A106KBHNNNE_C13585.html) | Act 12/01/23
1 | 10118194-0001LF/C | J2 | MicroXNJ_USB | Micro-B SMD | C404969 (https://www.lcsc.com/product-detail/USB-Connectors_SHOU-HAN-MicroXNJ_C404969.html)
2 | 10K | R1.1, R7.1 | R-EU_R1206 | R1206 | C17902 (https://www.lcsc.com/product-detail/Chip-Resistor-Surface-Mount_UNI-ROYAL-Uniroyal-Elec-1206W4F1002T5E_C17902.html) | Act 12/01/23
1 | 18K | R2.1 | R-EU_R1206 | R1206 | C2933614 (https://www.lcsc.com/product-detail/Chip-Resistor-Surface-Mount_FOJAN-FRC1206F1802TS_C2933614.html) | Act 12/01/23
1 | 1K2 | R11 | R-EU_R1206 | R1206 | C26035 (https://www.lcsc.com/product-detail/Chip-Resistor-Surface-Mount_UNI-ROYAL-Uniroyal-Elec-1206W4J0122T5E_C26035.html) | Act 12/01/23
2 | 1R | R9, R10 | R-EU_M1206 | M1206 | C17928 (https://www.lcsc.com/product-detail/Chip-Resistor-Surface-Mount_UNI-ROYAL-Uniroyal-Elec-1206W4F100KT5E_C17928.html) | Act 12/01/23
2 | 2K2 | R3.1, R5.1 | R-EU_R1206 | R1206 | C114933 (https://www.lcsc.com/product-detail/Chip-Resistor-Surface-Mount_YAGEO-RC1206FR-072K2L_C114933.html) | Act 12/01/23
3 | 4K7 | R4.1, R6.1, R12 | R-EU_R1206 | R1206 | C17936 (https://www.lcsc.com/product-detail/Chip-Resistor-Surface-Mount_UNI-ROYAL-Uniroyal-Elec-1206W4F4701T5E_C17936.html) | Act 12/01/23
1 | 4R7 | L1 | SRN6045-330M6045 | SRN6045 | C439386 (https://www.lcsc.com/product-detail/Power-Inductors_GLE-GCNR6045-4R7NC_C439386.html) | 4.7uH ±30%
1 | CR | LED2 | LED_REED | LED_0805 | C965812 (https://www.lcsc.com/product-detail/Light-Emitting-Diodes-span-style-background-color-ff0-LED-span_XINGLIGHT-XL-2012SURC_C965812.html)
1 | OK | LED3 | LED_GREN | LED_0805 | C965816 (https://www.lcsc.com/product-detail/Light-Emitting-Diodes-span-style-background-color-ff0-LED-span_XINGLIGHT-XL-2012SYGC_C965816.html)
Qty | Value | Parts | Device | Package | LCSC (https://www.lcsc.com/) | Others | Notes
| | | | THT

SMD

1 | MF-NSMF200 | F1.1 | PTCFUSE | 1812/1206 | C89656 (https://www.lcsc.com/product-detail/Resettable-Fuses_BOURNS-MF-NSMF200-2_C89656.html)
2 | SS34 | D1, D2.1 | DIODE_SCHOTTKY | DIODE_SMA | C3003045 (https://www.lcsc.com/product-detail/Schottky-Barrier-Diodes-SBD_HUXN-SS34_C3003045.html) | | Act 12/01/23
2 | BC847 | T1.1, T2.1 | BC847 | SOT23 | C57668 (https://www.lcsc.com/product-detail/Bipolar-Transistors-BJT_Nexperia-BC847B-215_C57668.html) | S8050 C2146 (https://www.lcsc.com/product-detail/Bipolar-Transistors-BJT_Jiangsu-Changjing-Electronics-Technology-Co-Ltd-S8050-J3Y_C2146.html) | Act 12/01/23
1 | TP5400 | U1 | TP5400 | ESOP8 | C24154 (https://www.lcsc.com/product-detail/Battery-Management-ICs_TOPPOWER-Nanjing-Extension-Microelectronics-TP5400_C24154.html)
2

The original document is made in ODS

WS2812B | NP1.1, NP2.1 | WS2812B | 5050-4 | C2843785 (https://www.lcsc.com/product-detail/Light-Emitting-Diodes-LED_XINGLIGHT-XL-5050RGBC-WS2812B_C2843785.html)

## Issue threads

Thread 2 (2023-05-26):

Error in NeoPixel THT?

PaddyCube, 2023-05-26:
Hello,

Ifound an error with the board layout. I use some WS2812D-THT LEDs I' not able to control.
According to your documentation, the flat side of LED needs to be faced to the edge of PCB.
When it gots soldered in this place, 5V and GND are swapped. If I rotate by 180deg. DIN and DOUT are swapped, so it will not work this way.

So you either need to swap 5V and GND, or DOUT and DIN

According to Documentation, I placed the LED so that flat side faces to PCB edge
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
This is the schematics I found for both, WS2811 and WS2812, the longest leg is VCC
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

Here you see that GND of LED is connected to VCC of shield
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

I'll try to solder a new LED and bending the pins.

Thanks so far for this cool project. My kids now can program their own robot and I've learned how to solder SMD

xdesig, 2023-05-26:
I think you mean "You have found a problem with the Neopixel 5mm". When I
designed that board I made sure of the pins of those Neopixels. Now you can
find manufacturers that exchange pins, sorry for the inconvenience. The
neopixels that I have follow the Din, Vcc, GND, Dout norm

O ven., 26 de maio de 2023 ás 13:04, PaddyCube ***@***.***>)
escribiu:

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

PaddyCube, 2023-05-28:
I'll close this issue. I solved it by swapping VCC and GND pin by bending before soldering. I assume you add some note to documentation so others are aware of this. Maybe you already added a note to spain description but at least me, I had to use google translate to understand.

xdesig, 2023-05-28:
Hi Paddy.
We will be able to locate the most common neopixels now and do something to
fix this.
 Thank you.
 I would also like to translate the manual into English ( time to time)

Best regards
 Xabier Rosas

O dom., 28 de maio de 2023 ás 11:08, PaddyCube ***@***.***>)
escribiu:

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

Closed 2023-05-28.

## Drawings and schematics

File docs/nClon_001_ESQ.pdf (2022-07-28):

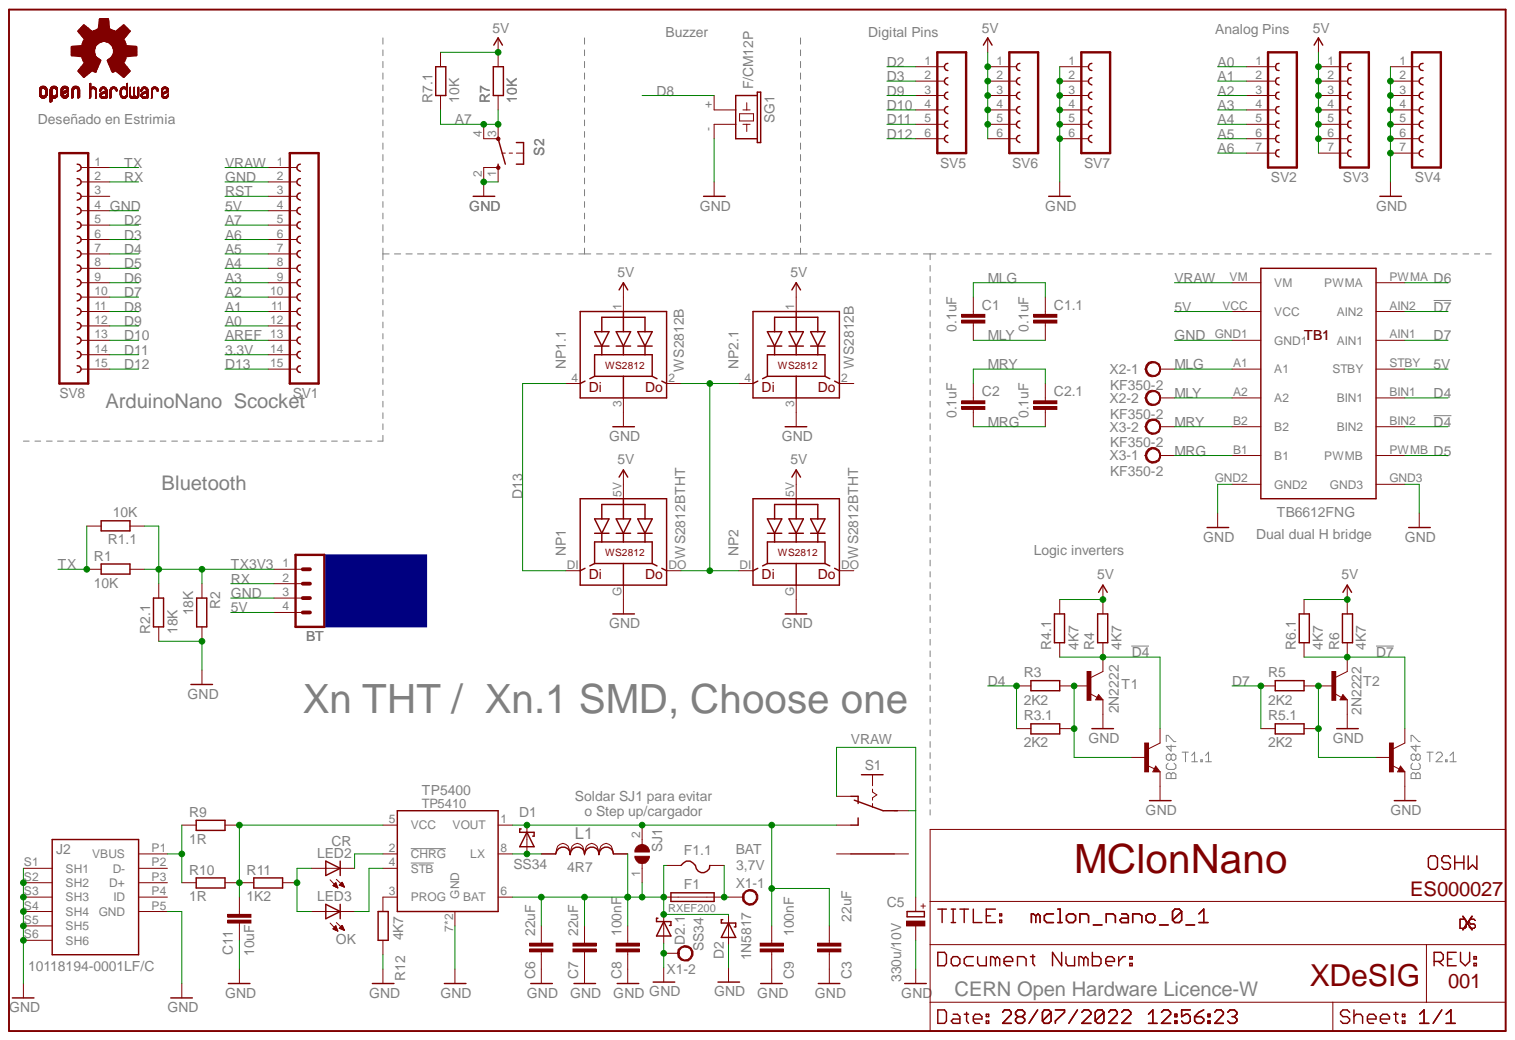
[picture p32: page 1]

GND GND

CERN Open Hardware Licence-W

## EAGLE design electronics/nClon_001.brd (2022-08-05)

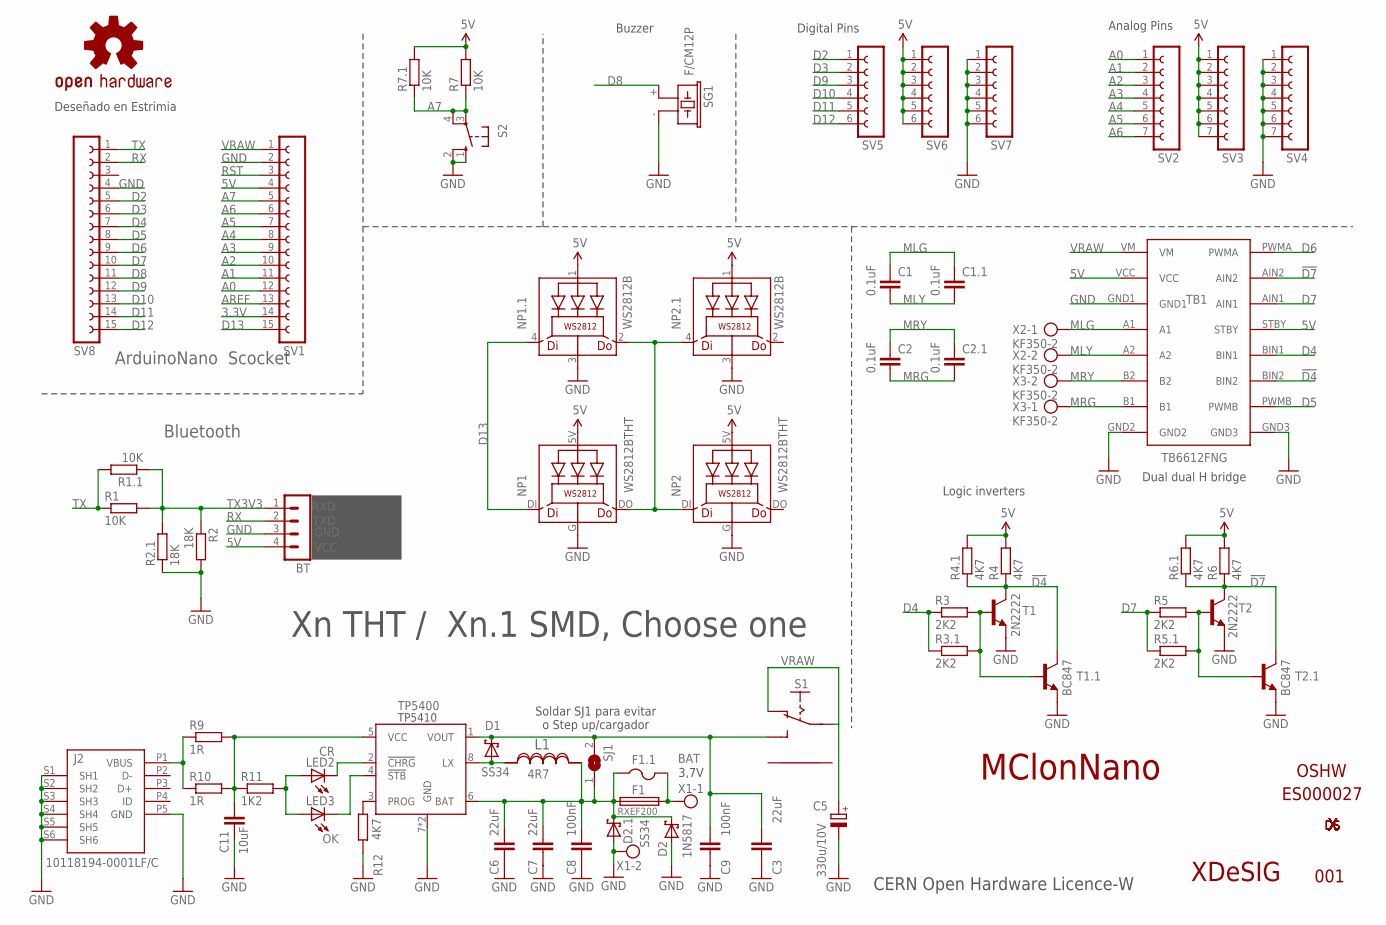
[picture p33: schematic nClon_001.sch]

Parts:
BT: MA04-1
C1, C2: 0.1uF; C050-024X044
C1.1, C2.1: 0.1uF; C1206
C3, C6, C7: 22uF; C1206
C5: 330u/10V; E2,5-6
C8, C9: 100nF; C1206
C11: 10uF; C1206
D1, D2.1: SS34; DIODE_SMA
D2: 1N5817; DO35-7
F1: RXEF200; TE5
F1.1: MF-NSMF200; 1812
J2: 10118194-0001LF/C; SMARTPRJ_CON2_USB_MICRO_B_AT
L1: 4R7; SRN6045
LED2: CR; CHIPLED_0805
LED3: OK; CHIPLED_0805
LOGO4: OSHW-LOGOS; OSHW-LOGO-S
NP1, NP2: WS2812BTHT; NEOPIXEL5MM
NP1.1, NP2.1: WS2812B; 5050-4
R1, R7: 10K; 0204/7
R1.1, R7.1: 10K; R1206
R2: 18K; 0204/7
R2.1: 18K; R1206
R3, R5: 2K2; 0204/7
R3.1, R5.1: 2K2; R1206
R4, R6: 4K7; 0204/7
R4.1, R6.1, R12: 4K7; R1206
R9, R10: 1R; M1206
R11: 1K2; R1206
S1: ESCORNA_SK12F14D; ESCORNA_SK-12D07
S2: 10-XX; B3F-10XX
SG1: F/CM12P
SJ1: JUMPER_SJW
SV1, SV8: CON-LSTA_FE15-1; CON-LSTA_FE15
SV2, SV3, SV4: FE07-1; FE07
SV5, SV6, SV7: FE06-1; FE06
T1, T2: 2N2222; TO92-EBC-OVAL
T1.1, T2.1: BC847; SOT23
TB1: TB6612FNG
U1: TP5400; ESOP8
U$7: OSHW
U$8, U$19: XDESIG5MM; XDESIG_CU
U$18: XDESIG21; XDESIG
X1, X2, X3: KF350-2; AK550/2

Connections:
3.3V: SV1.14
5V: BT.4, NP1.5V (LEDVDD), NP1.1.1 (LEDVDD), NP2.5V (LEDVDD), NP2.1.1 (LEDVDD), R4.2, R4.1.2, R6.2, R6.1.2, R7.2, R7.1.2, SV1.4, SV3.1, SV3.2, SV3.3, SV3.4, SV3.5, SV3.6, SV3.7, SV6.1, SV6.2, SV6.3, SV6.4, SV6.5, SV6.6, TB1.STBY, TB1.VCC
!D4: R4.1, R4.1.1, T1.C, T1.1.3 (C), TB1.BIN2
!D7: R6.1, R6.1.1, T2.C, T2.1.3 (C), TB1.AIN2
A0: SV1.12, SV2.1
A1: SV1.11, SV2.2
A2: SV1.10, SV2.3
A3: SV1.9, SV2.4
A4: SV1.8, SV2.5
A5: SV1.7, SV2.6
A6: SV1.6, SV2.7
A7: R7.1, R7.1.1, S2.3, S2.4 (P1), SV1.5
AREF: SV1.13
BAT: C6.1, C7.1, C8.1, D2.C, D2.1.C, F1.1, F1.1.1, L1.1, SJ1.1, U1.6 (BAT)
D2: SV5.1, SV8.5
D3: SV5.2, SV8.6
D4: R3.1, R3.1.1, SV8.7, TB1.BIN1
D5: SV8.8, TB1.PWMB
D6: SV8.9, TB1.PWMA
D7: R5.1, R5.1.1, SV8.10, TB1.AIN1
D8: SG1.+ (1), SV8.11
D9: SV5.3, SV8.12
D10: SV5.4, SV8.13
D11: SV5.5, SV8.14
D12: SV5.6, SV8.15
D13: NP1.DI, NP1.1.4 (DI), SV1.15
GND: BT.3, C3.2, C5.-, C6.2, C7.2, C8.2, C9.2, C11.2, D2.A, D2.1.A, J2.P5 (GND), J2.S1 (SH1), J2.S2 (SH2), J2.S3 (SH3), J2.S4 (SH4), J2.S5 (SH5), J2.S6 (SH6), NP1.G (GND), NP1.1.3 (GND), NP2.G (GND), NP2.1.3 (GND), R2.2, R2.1.1, R12.1, S2.1 (S), S2.2 (S1), SG1.- (2), SV1.2, SV4.1, SV4.2, SV4.3, SV4.4, SV4.5, SV4.6, SV4.7, SV7.1, SV7.2, SV7.3, SV7.4, SV7.5, SV7.6, SV8.4, T1.E, T1.1.2 (E), T2.E, T2.1.2 (E), TB1.GND1, TB1.GND2, TB1.GND3, U1.7 (GND), U1.9 (GND), X1.2
MLG: C1.1, C1.1.1, TB1.A1, X2.1
MLY: C1.2, C1.1.2, TB1.A2, X2.2
MRG: C2.2, C2.1.2, TB1.B1, X3.1
MRY: C2.1, C2.1.1, TB1.B2, X3.2
unnamed: R3.2, R3.1.2, T1.B, T1.1.1 (B)
unnamed: F1.2, F1.1.2, X1.1
unnamed: R5.2, R5.1.2, T2.B, T2.1.1 (B)
unnamed: LED2.A, LED3.A, R11.2
unnamed: LED2.C, U1.2 (!CHRG)
unnamed: NP1.DO, NP1.1.2 (DO), NP2.DI, NP2.1.4 (DI)
unnamed: D1.A, L1.2, U1.8 (LX)
unnamed: LED3.C, U1.4 (!STB)
unnamed: R12.2, U1.3 (PROG)
RST: SV1.3
RX: BT.2, SV8.2
TX: R1.1, R1.1.2, SV8.1
TX3V3: BT.1, R1.2, R1.1.1, R2.1, R2.1.2
VBUS: J2.P1 (VBUS), R9.1, R10.1
VCC: C3.1, C9.1, D1.C, S1.P$3 (S), SJ1.2, U1.1 (VOUT)
VCH: C11.1, R9.2, R10.2, R11.1, U1.5 (VCC)
VRAW: C5.+, S1.P$1, S1.P$2 (O), SV1.1, TB1.VM

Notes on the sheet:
MClonNano
001
Bluetooth
RXD
TXD
GND
VCC
XDeSIG
Digital Pins
Analog Pins
Dual dual H bridge
Logic inverters
Deseñado en Estrimia
ArduinoNano Scocket
3,7V
Soldar SJ1 para evitar o Step up/cargador
TP5400
CERN Open Hardware Licence-W
Buzzer
Xn THT / Xn.1 SMD, Choose one
TP5410
ES000027

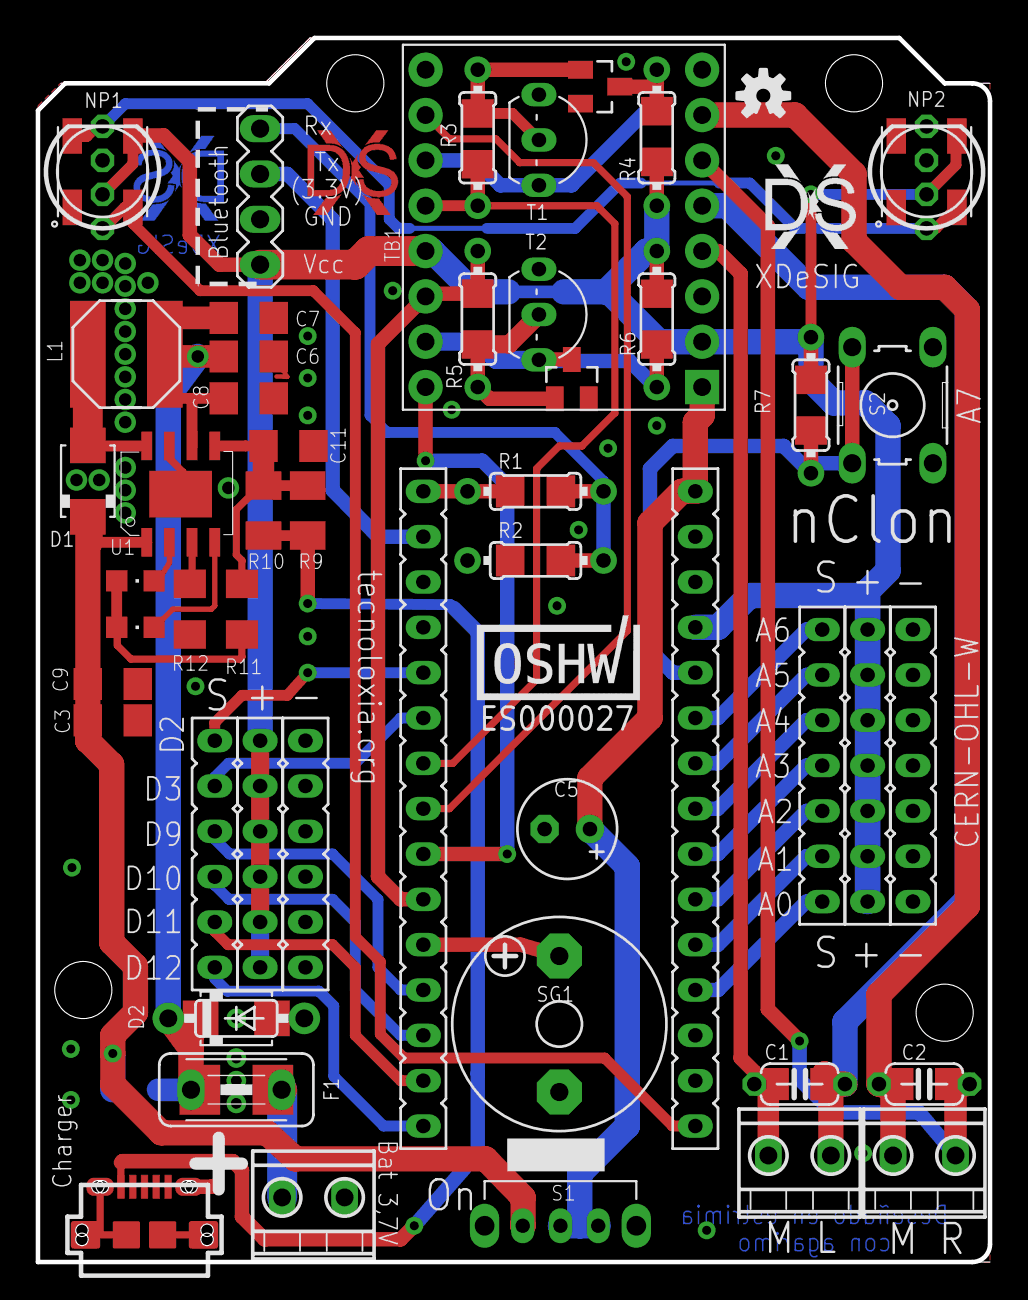
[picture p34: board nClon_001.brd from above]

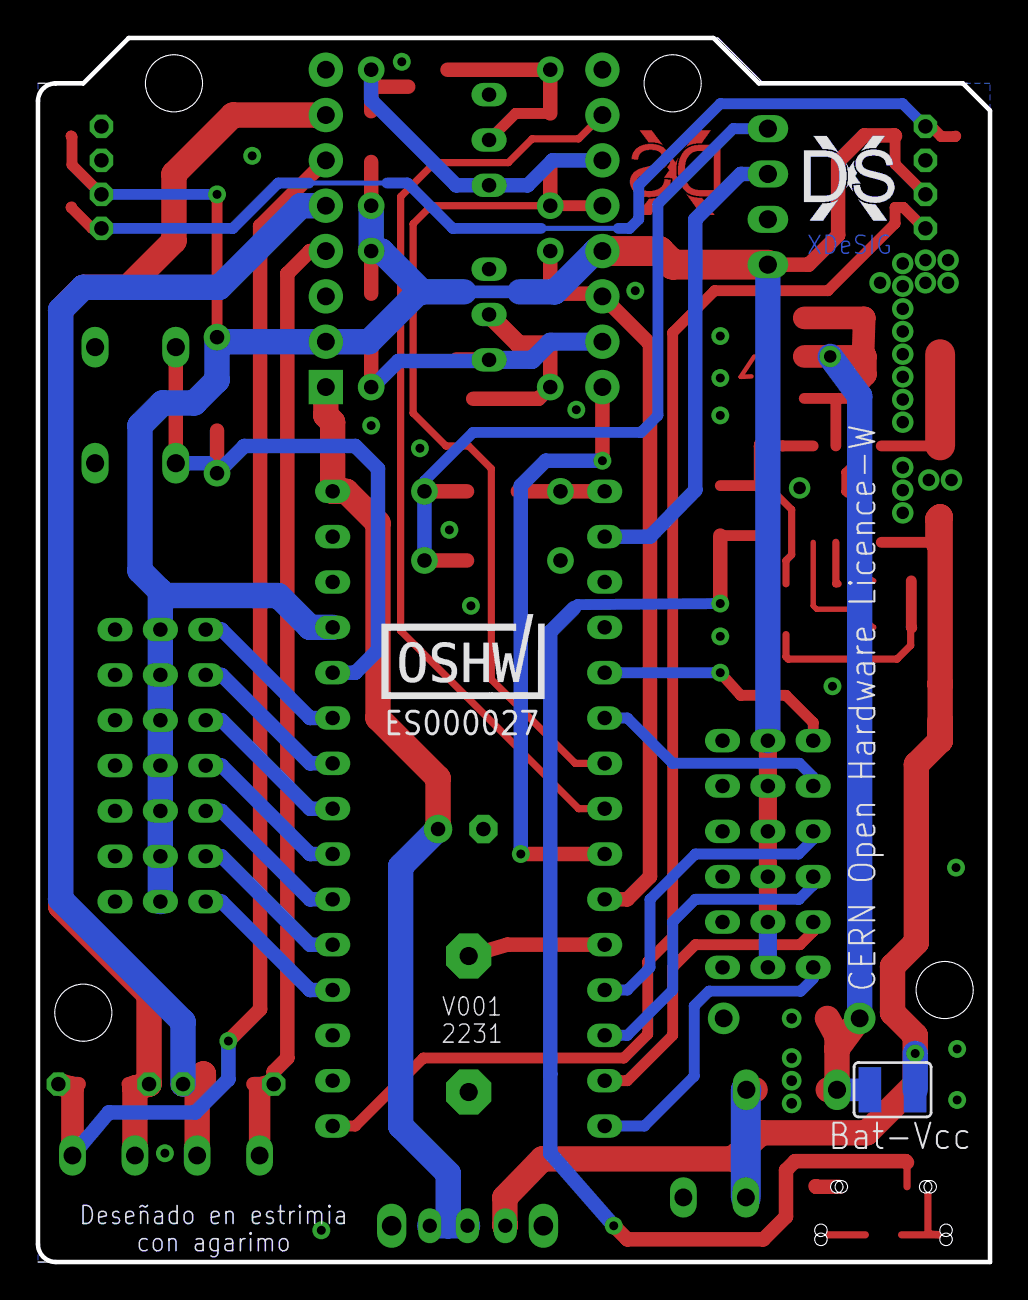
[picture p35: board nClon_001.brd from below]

Board: 2 copper layers, 53.3 x 68.6 mm, 71 parts (4 on the bottom side), 45 nets.

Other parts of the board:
U$2: OSHW
U$21: XDESIG21; XDESIG

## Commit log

2022-06-04 Update img
    [mclon_nano_0_1.brd, mclon_nano_0_1.sch]
2022-06-16 update gerber
2023-01-12 Update components link
    [nClon_001_BOM.ods, nClon_001_BOM.xls, nClon_001_BOM.xlsx]
2023-01-12 Updating missing component links
    [nClon_001_BOM.ods, nClon_001_BOM.xls]

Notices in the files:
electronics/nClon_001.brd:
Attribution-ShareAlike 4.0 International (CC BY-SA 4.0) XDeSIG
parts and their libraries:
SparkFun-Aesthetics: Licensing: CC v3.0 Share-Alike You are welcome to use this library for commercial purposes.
